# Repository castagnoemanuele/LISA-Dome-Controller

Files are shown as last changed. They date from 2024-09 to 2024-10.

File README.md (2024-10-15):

# LISA-Dome-Controller
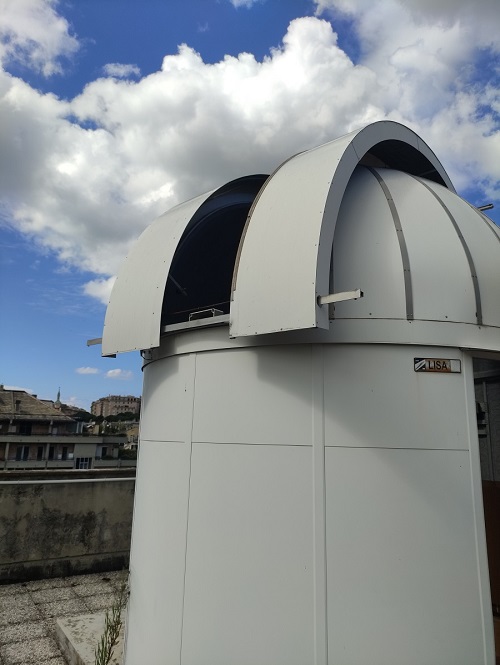
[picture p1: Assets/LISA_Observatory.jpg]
Observatory


This repository contains the project of the controller system for the LISA observatory, located in Genoa. The old controller board was defective and needed to be replaced, and by doing that the system was also modernized and updated to support, for example, the WiFi connection. 

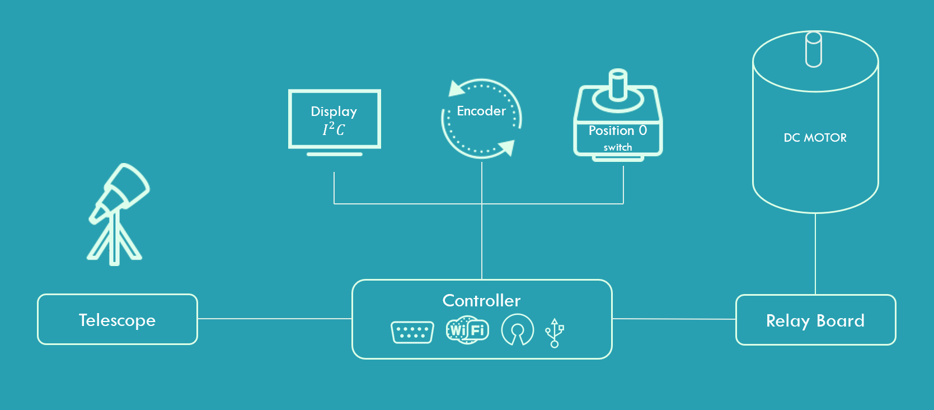
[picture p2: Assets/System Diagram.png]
Diagram

The system is composed of three main sub-systems:
* Telescope
* Motor system
* Control system

## Motor system
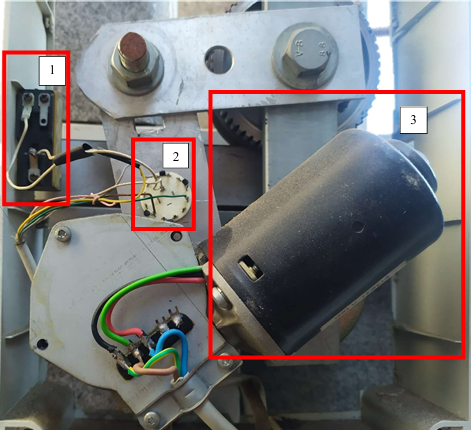
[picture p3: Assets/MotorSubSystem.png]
Motor System


The motor system is composed of three parts:
1. End switch: a simple switch that gets closed at a certain position, which will be referred as "position zero" from now on.
2. Encoder: has three pins (ENCODER1, ENCODER2, ENCODER3) plus a common one. Each one is activated every third of a rotation of the motor
3. 12V DC motor (60w power draw)

The only modification done to this part of the system was a RC circuit connected in parallel with the end switch to filter out noise that was causing problems (ghost change of state of the end switch).
The rotative encoder functioning is is simplified in the following animation:

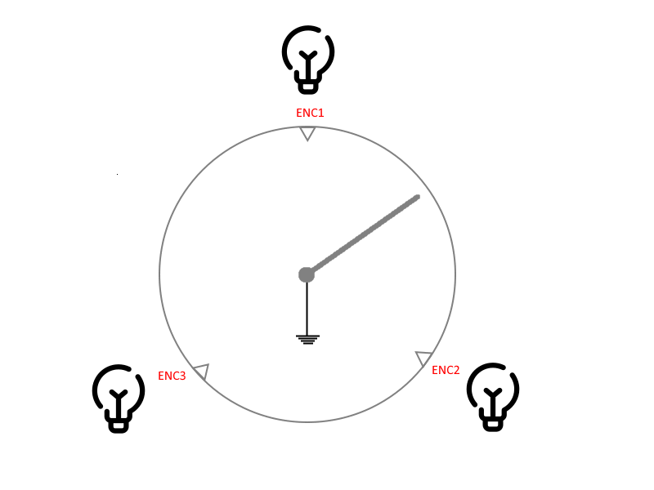
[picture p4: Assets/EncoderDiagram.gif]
Encoder_rotation


In the way it works it is more similar to a rotation counter, but given it's function it will be called encoder.

## Controller system

Composed of four parts:
* Two 12V power supplies, one for the motor and one for the Control system
* The controller board
* The relay board
* The external interface

Here is a more complete overview on the contents of the electrical box:

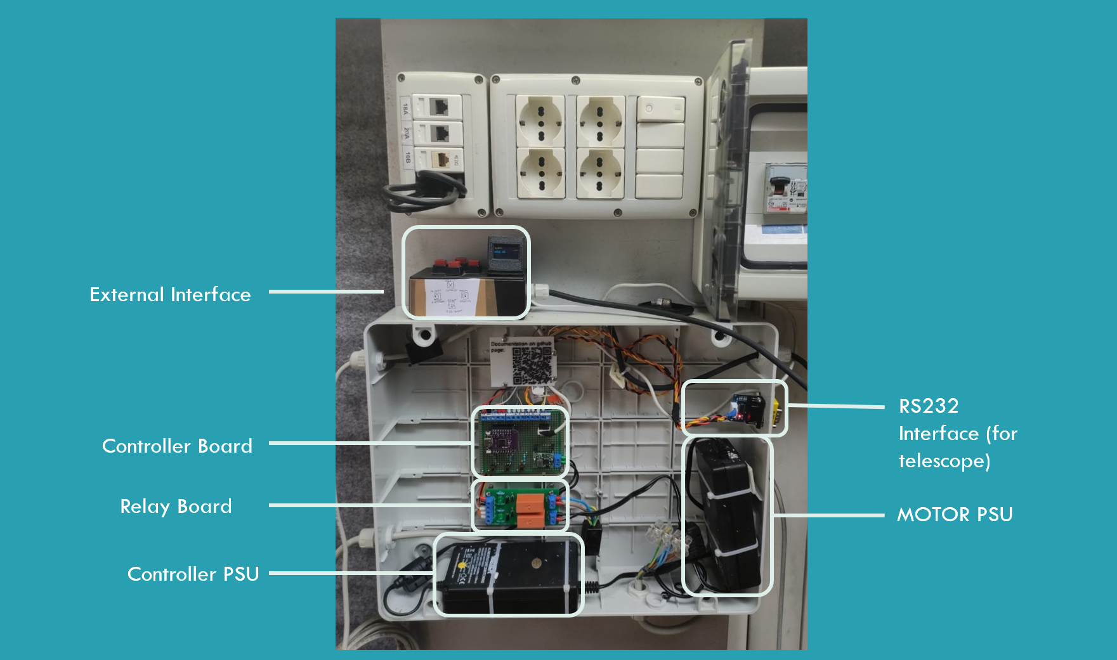
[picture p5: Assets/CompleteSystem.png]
Controller overview


### Relay board
This board has been developed for the purpose of powering the 12V motor. In needs to be able to switch the direction, so two SPDT relays have been used to form an h-bridge. The microcontroller drives the relays throught two npn transistors, and two LEDs have been added to signal which relay is active. The connections are the following:
| PIN | Description|
| ----|---|
|S1 |Selector pin for relay 1, when HIGH turns the coil of relay 1 on|
|S2 |Selector pin for relay 2, when HIGH turns the coil of relay 2 on|
|GND  |Ground, connected to the gnd of the step down on the control board (note that it is isolated from the 12V part of the circuit) 
|5V | Connected to the output of the step down on the control board
|GND(High power part)|Connected to the motor power supply|
|12V | Connected to the motor power supply|
|MOTOR| connection to the motor

The board was custom made using EasyEda and printed by JLCPCB. the PCB has copper traces wide and thick enough to support more than 5A of current. Schematics are avaiable on the apposite folder of this repo.

#### Components of the Relay Board
* 2* RT114005 SPDT relays
* 2* 2N2222 transistors
* 2*220 Ohm Resistor
* 2*1KOhm Resistor
* 2* Flyback diode
* Screw terminal connectors

### Controller board
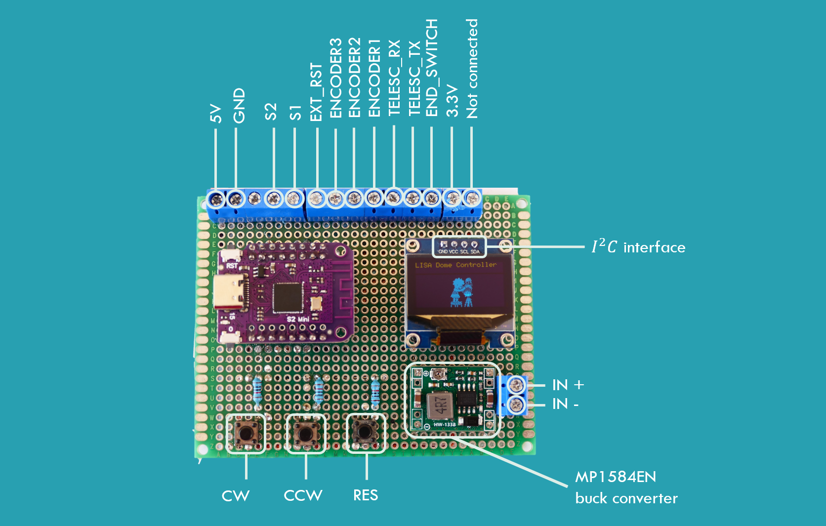
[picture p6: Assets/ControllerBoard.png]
Controller Board Diagram


The controller board hosts the microcontroller and all the interfaces it needs to check the sensors and control the other devices in the system. It also hosts three buttons, which have the same functionality as the ones in the external interface. The microcontroller is a WEMOS ESP32-S2 mini, chosen for the low cost and WiFi support.
the power supply that was present in the electrical box had an output of 12V DC, so a variable step down converter was added, and it is set to 5V and connected to the Vin pin of the microcontroller. 
The I²C interface is powered from the 3.3V pin of the microcontroller and has two 10K pullup resistors, on the back of the perf board.
All the connections are reported in the schematic on the apposite folder. The pinscan be described as it follows:

| PIN | Description|
| ----|---|
|5V| Connection to the Vin pin of the MCU and the OUT+ of the buck converter|
|GND| Ground =0|
|S2 | Connected to the S2 Pin of the relayboard. When high activates relay 2. It is also connected to the External S2 Button of the physical interface|
|S1 | Connected to the S2 Pin of the relayboard. When high activates relay 1. It is also connected to the External S1 Button of the physical interface|
|EXT_RST| Connected to the reset Button of the external interface
|Encoder1,2,3| Connected to the encoder pins (in the motor system|
|TELESC_RX| Connected to the RX pin of the serial to RS232 Adapter|
|TELESC_TX| Connected to the TX pin of the serial to RS232 Adapter|
|END_SWITCH| Connected to the end switch in the motor system!
|3.3V| Connected to the 3.3V pin of the ESP32|
|IN+| Positive Input pin for the buck converter. In the system connected to a 12V PSU|
|IN-| Negative pin for the buck converter. In the system connected to a 12V PSU|

### External interface
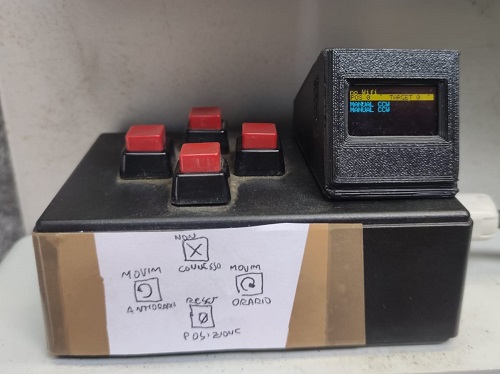
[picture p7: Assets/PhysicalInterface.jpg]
External Interface


The buttons present on the controller board are not avaiable when the electrical box is closed, so to be able to control the Dome posision manually it was necessary to connect the (already present) external keypad and add the external display with a 3d printed enclosure, which was posted on [Thingiverse](https://www.thingiverse.com/thing:3080488) by SteveTecx.

## Notes
The .ino file in the simulator folder was used to simulate the behaviour of the dome to program the firmware outside of the dome. More details are available in my thesis pdf file in the documents folder.

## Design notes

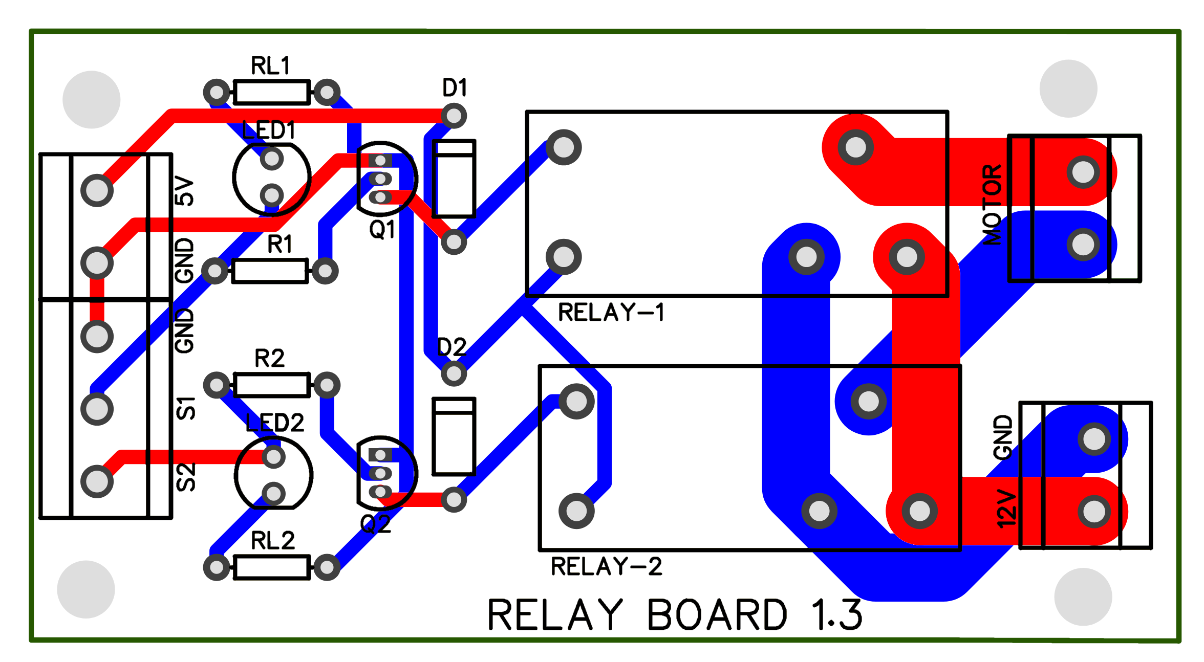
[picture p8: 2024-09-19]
Schematics/RelayBoard schematic .png

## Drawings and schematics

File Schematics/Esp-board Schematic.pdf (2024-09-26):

+3.3V

+3.3V

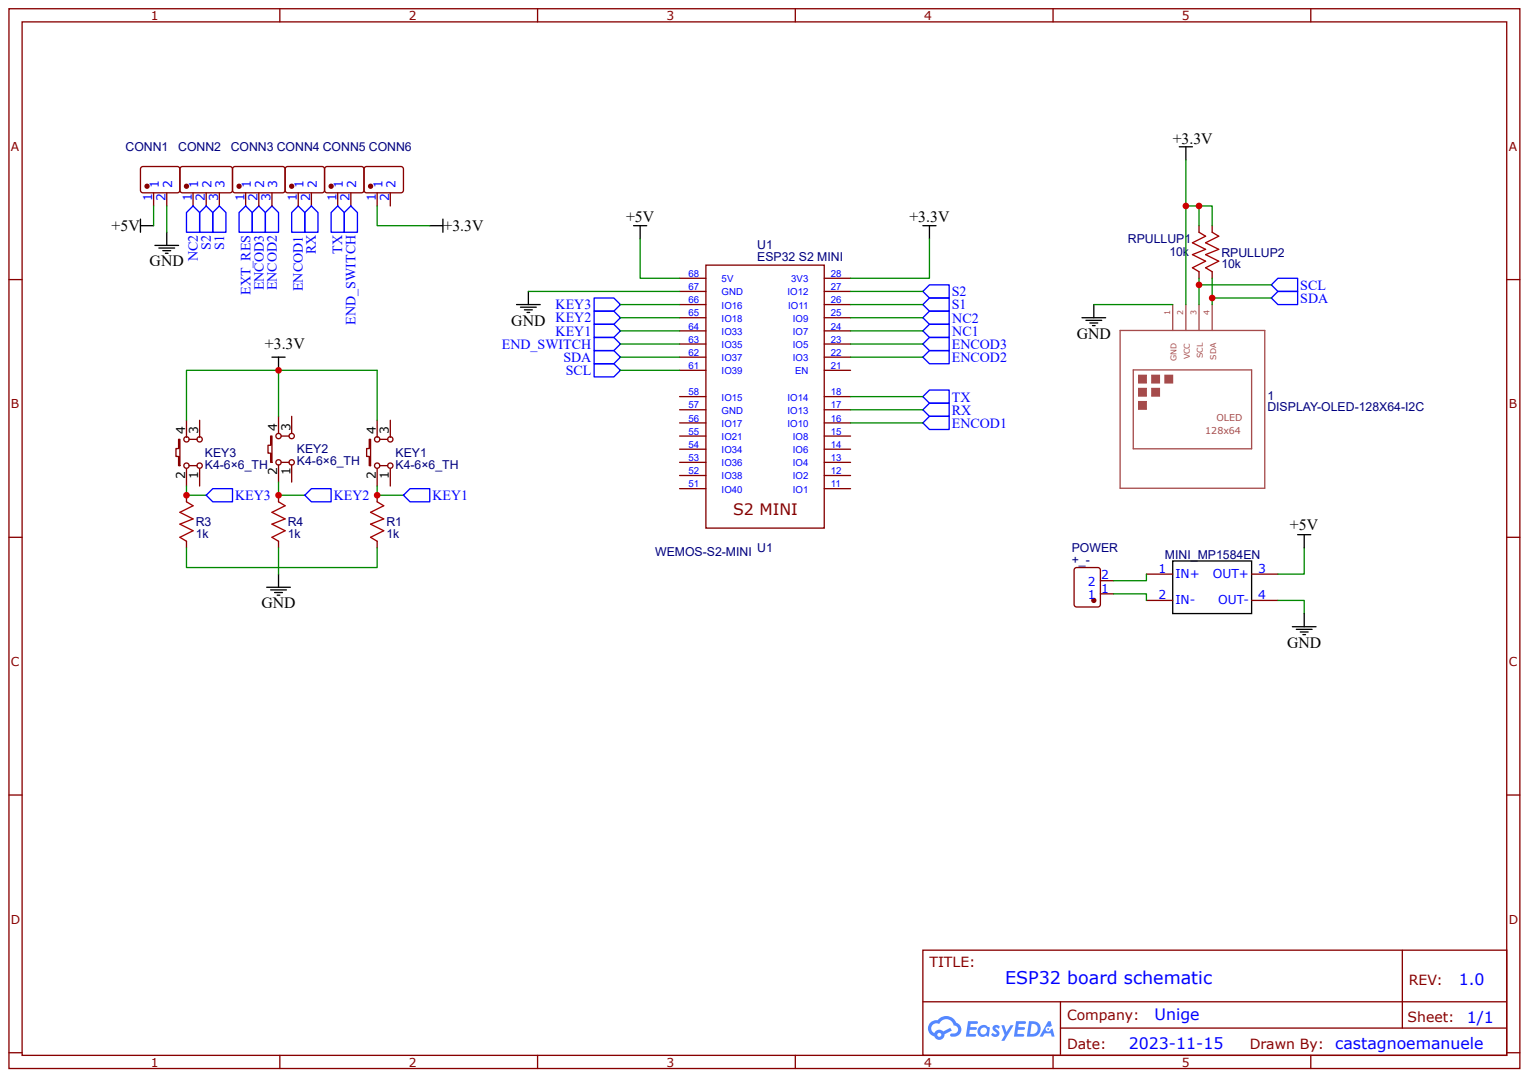
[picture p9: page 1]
TITLE:; ESP32 board schematic; REV: 1.0; Date:; Sheet: 1/1; Company: Unige; ESP32 S2 MINI; WEMOS-S2-MINI U1; S2 MINI; GND; KEY1; KEY2; KEY3; CONN2; DISPLAY-OLED-128X64-I2C; VCC; SCL; SDA; OLED; MINI_MP1584EN IN+; OUT+; OUT- 4; POWER; ENCOD2; ENCOD3; ENCOD1; ENCOD3 ENCOD2; RPULLUP2; RPULLUP1; SCL SDA; END_SWITCH; CONN3; EXT_RES; CONN1; CONN4; CONN5; CONN6; TX END_SWITCH

Drawn By: castagnoemanuele

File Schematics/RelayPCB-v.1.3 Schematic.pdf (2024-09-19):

+5V

+12V | +12V

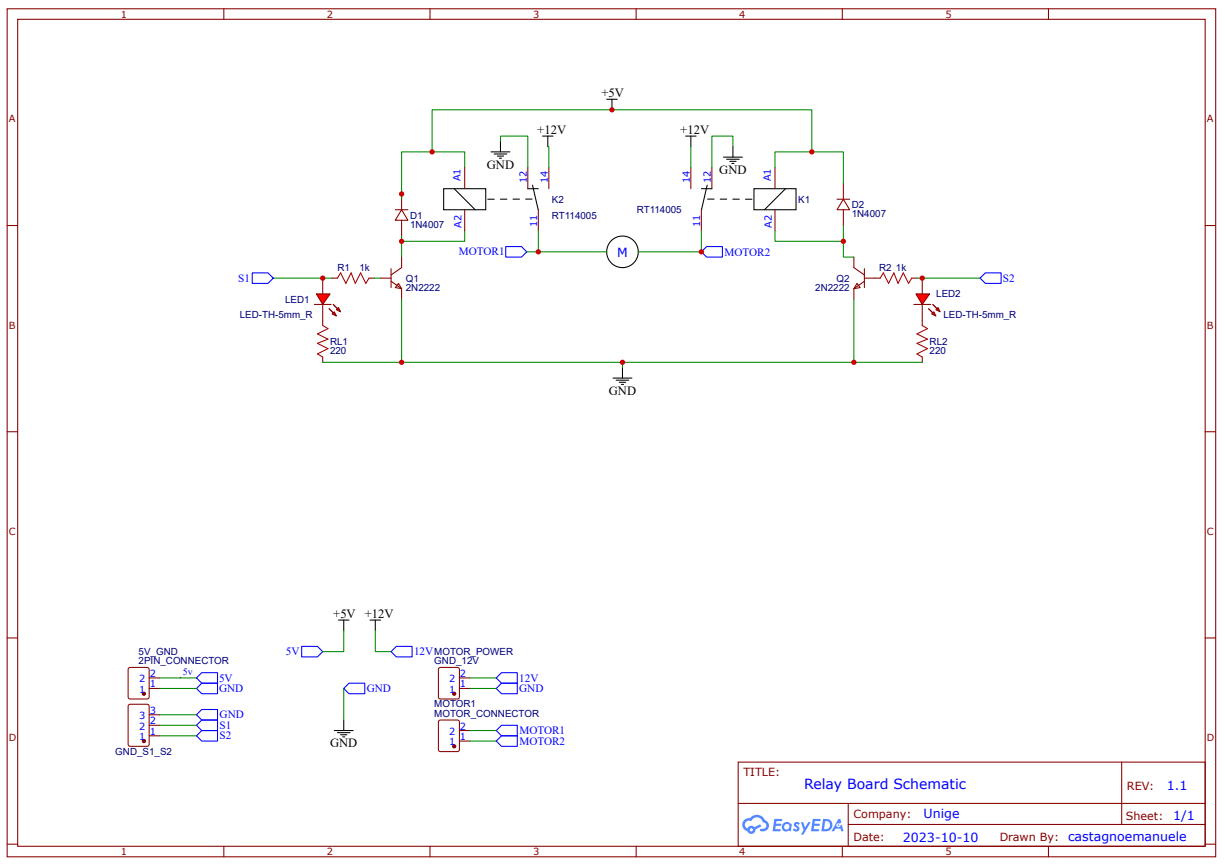
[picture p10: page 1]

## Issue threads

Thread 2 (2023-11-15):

Problem: encoder non being monitored during manual control

castagnoemanuele, 2023-11-15:

Closed 2023-11-20.

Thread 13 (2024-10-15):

Communication with telescope implemented but not functioning

castagnoemanuele, 2024-10-15:
In the `telescope.cpp` file a simple function `checkTelescopePosition` has been implemented to send a request message to the encoder, which should get interpreted by the telescope, which should respond with his position, according to the MEADE serial comm. protocol.

When testing with my computer, I could see that the request message was being sent correctly, and if I replied from my computer with the correctly formatted position, the microcontroller was able to interpret and save the data. This means that at least the physical connection should be working (it has to be noted that to interface the RS232 serial to the computer a USB adapter has been used, but it is not present when the direct connection between the microcontroller and telescope is made).

At the same time, if by using the USB to RS232 serial adapter I send the position request to the telescope (which is `:GR#`) I get the correct data from the telescope, which shoul mean that the telescope is working and also the request is the right one.

The following image is a screenshot of the serial monitor that i opened from my computer to the telescope, and it shows the telescope responding to the request of the position,as stated above.

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

The issue is that when I connect the microcontroller to the telescope and start the telescope position request function (from the serial monitor of the microcontroller's usb port, by typing the letter `p` **no data gets received by the microcontoller**, and after the timeout the execution continues normally.

Things i tried already:

-  Checking physical connection with a multimeter (also voltages)
- adding a `\n` after the `:GR#` message request
-  Checking if the baud rate is set correctly
-  Different serial port

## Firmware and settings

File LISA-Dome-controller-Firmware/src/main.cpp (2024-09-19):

#include <WiFi.h>
#include <WebServer.h>
#include <SPI.h>
#include <Wire.h>
#include <Adafruit_GFX.h>
#include <Adafruit_SSD1306.h>
#include <encoder.h>
#include <config.h>
#include <WiFiManager.h>
#include <telescope.h>
#include <button.h>
#include <Preferences.h>
#include <displayOled.h>


Preferences preferences;
WebServer server(80);

Telescope LISA;
Encoder encoder = {0,0,false,0,0,0,UNKNOWN};


Adafruit_SSD1306 display(SCREEN_WIDTH, SCREEN_HEIGHT, &Wire, OLED_RESET); //initialization of Oled Screen
DisplayOled displayOled;


Button bttReset = {BTT_RST, 0, false,"RESET"};///onboard button to reset the dome's position
Button bttExternalReset = {BTT_EXT_RST, 0, false,"RESET"}; ///external button to reset the dome's position
Button bttClockwise = {BTT_CW, 0, false,"MANUAL CW"};
Button bttCounterClockwise = {BTT_CCW, 0, false,"MANUAL CCW"};
Button limitSwitch = {BTT_END, 0, false, "END REACHED"};


bool needUpdate = false; //flag to update the display only when the button is pressed
static bool commandsPrinted = false; //bool for user interface commands

/// @brief Interrupt Routine handler, sets .pressed attribute according to the reading
/// @return 
void IRAM_ATTR bttClick() {
  bttReset.pressed = digitalRead(BTT_RST);
  bttExternalReset.pressed = digitalRead(BTT_EXT_RST);
  bttClockwise.pressed = digitalRead(BTT_CW);
  bttCounterClockwise.pressed = digitalRead(BTT_CCW);
  limitSwitch.pressed = !digitalRead(BTT_END); //opposite because it is active when low
  needUpdate= true;
}


void IRAM_ATTR encoderTick() {
  encoder.hasChanged=true;
}


bool dataSaveNecessary=false;
bool telescopeCheckNecessary=false;
hw_timer_t *timerEPROM = NULL;
hw_timer_t *timerTelescope = NULL;

/// @brief Interrupt Routine handler, Checks the timer to save the position periodically
void IRAM_ATTR onTimerEPROM(){
  dataSaveNecessary=true;
}
/// @brief Interrupt Routine handler, Checks the timer to check the telescope position periodically
void IRAM_ATTR onTimerTelescope(){
  telescopeCheckNecessary=true;
}


void setup()
{
  ////////////////////////SERIAL COMMUNICATION INIT/////////////////////
  Serial.begin(9600); 
  Serial1.begin(9600,SERIAL_8N1,TX_PIN,RX_PIN); ///serial port to communicate with telescope
  /////////////////BUTTON/PIN INITIALIZATION////////////////////////////
  pinMode(LED_BUILTIN, OUTPUT);      // set the LED pin mode
  pinMode (bttReset.PIN, INPUT_PULLDOWN);
  pinMode (bttExternalReset.PIN, INPUT_PULLDOWN);
  pinMode (bttClockwise.PIN, INPUT_PULLDOWN);
  pinMode (bttCounterClockwise.PIN, INPUT_PULLDOWN);
  pinMode (limitSwitch.PIN, INPUT_PULLUP);
  pinMode (S1_PIN, OUTPUT);
  pinMode (S2_PIN,OUTPUT);
  digitalWrite(S1_PIN, LOW);
  digitalWrite(S2_PIN, LOW);
  
  attachInterrupt (limitSwitch.PIN, bttClick, FALLING);
  attachInterrupt (bttReset.PIN, bttClick, CHANGE);
  attachInterrupt (bttClockwise.PIN, bttClick, CHANGE);
  attachInterrupt (bttCounterClockwise.PIN, bttClick, CHANGE);
  attachInterrupt (bttExternalReset.PIN, bttClick, CHANGE);
  /////////////////////////ENCODER PINS INITIALIZATION////////////////////////////////
  pinMode(ENCODER1, INPUT_PULLUP);
  pinMode(ENCODER2, INPUT_PULLUP);
  pinMode(ENCODER3, INPUT_PULLUP); 
  attachInterrupt(digitalPinToInterrupt(ENCODER1), encoderTick, FALLING);
  attachInterrupt(digitalPinToInterrupt(ENCODER2), encoderTick, FALLING);
  attachInterrupt(digitalPinToInterrupt(ENCODER3), encoderTick, FALLING);

  ////////////////////////OLED INITIALIZATION//////////////////////////
  displayOled.initDisplay(display, encoder, LISA);

    ////////////////////////////WIFI INITIALIZATION//////////////////////////
    // start by connecting to a WiFi network
    //WiFiManager wifiManager; //REMOVED AFTER INITIAL SETUP
    //wifiManager.resetSettings(); //TO CLEAN SETTINGS
    //wifiManager.autoConnect("AutoConnectAP");
    

    ///Wait for Connection while also printing on the display
    // for (int i = 0; i<12;i++)
    // {
    //   if (WiFi.status() != WL_CONNECTED) {
    //     delay(500);
    //     Serial.print(".");
    //     displayMessage("......");
    //   }
    // }

  if (WiFi.status() == WL_CONNECTED) 
  {
    //Blink 3 times to signal wifi connection
    for (int i=0; i<3; i++){
      digitalWrite(LED_BUILTIN, HIGH);
      delay(200);
       digitalWrite(LED_BUILTIN, LOW);
      delay(100);
    }
    
    
    Serial.println("");
    Serial.println("WiFi connected.");
    Serial.println("IP address: ");
    Serial.println(WiFi.localIP());
    
  }
  else{displayOled.FirstRow="no Wifi";}
  
  ////////////////////////ENCODER STATUS SETUP//////////////////////////////
  preferences.begin("LISA", true); //start preferences in readonly mode
  encoder.currentPosition = preferences.getInt("currentPosition", 0); //read values from EPROM and set them to the encoder variables
  encoder.fullRotation= preferences.getInt("fullRotation",0);
  //check if we have any data on the fullRotation
  if(encoder.fullRotation==0){
    Serial.println("No full rotation data found, counting now");
    displayOled.displayMessage("COUNT TICKS",display);
    countTicksFullRotation(encoder,bttReset,limitSwitch,preferences);
  }
  Serial.print("Current position: ");
  Serial.println(encoder.currentPosition);
  encoder.currentDegrees = convertTicksToDegrees(encoder.currentPosition, encoder);
  Serial.print("     In degrees: ");
  Serial.println(encoder.currentDegrees);
  Serial.print("Number of encoder clicks for a full rotation: ");
  Serial.println(encoder.fullRotation);
  preferences.end();

  displayOled.printPositionStatus(display, encoder, LISA); //refresh position with the new data from the EPROM

  ////////////////////////////TIMER FOR SAVING DATA/////////////////////////////
  timerEPROM = timerBegin(0, 8000, true);
  timerAttachInterrupt(timerEPROM, &onTimerEPROM, true);
  timerAlarmWrite(timerEPROM, 3000000, true); //setting a timer to save encoder data to EPROM every 5 minutes
  timerAlarmEnable(timerEPROM); //Just Enable the timer

  //////////////////////////TIMER FOR TELESCOPE CHECK//////////////////////////
  timerTelescope = timerBegin(1, 8000, true);
  timerAttachInterrupt(timerTelescope, &onTimerTelescope, true);
  timerAlarmWrite(timerTelescope, 100000, true); //setting a timer to check the telescope position every 10 seconds
  //timerAlarmEnable(timerTelescope); //Just Enable the timer

  

}

void loop()
{
  if (limitSwitch.pressed)
  {
    if(encoder.currentPosition!=0){
      Serial.println("End of run reached");
    }
    encoder.currentPosition = 0;
    encoder.currentDegrees = 0;
  }
  ////////////////////////////MANUAL CONTROL///////////////////////////
  //when the reset button is pressed, the motor starts spinning clockwise until the limit switch stops it
  if (bttReset.pressed || bttExternalReset.pressed)
  {
    displayOled.displayMessage(bttReset.message,display);
    resetPosition(encoder, bttReset, limitSwitch);
    displayOled.displayMessage("END of RUN",display);
    displayOled.printPositionStatus(display, encoder, LISA);
  }
  //turn on relays according to the button status
  digitalWrite(S1_PIN, bttClockwise.pressed);
  digitalWrite(LED_BUILTIN, bttClockwise.pressed);

  if (bttClockwise.pressed & needUpdate)
  {
    displayOled.displayMessage(bttClockwise.message,display);
    needUpdate = false;
  }
  digitalWrite(S2_PIN, bttCounterClockwise.pressed);
  digitalWrite(LED_BUILTIN, bttCounterClockwise.pressed);
  if (bttCounterClockwise.pressed & needUpdate)
  {
    displayOled.displayMessage(bttCounterClockwise.message,display);
    needUpdate = false;
  }
  ///////////////////////UPDATE POSITION//////////////////////////////
  if (encoder.hasChanged)
  {
    //when movement is detected, we first check the direction, and then update the position
    checkEncoder(encoder);
    encoder.hasChanged = false;
    updatePosition(encoder);
    displayOled.printPositionStatus(display, encoder, LISA);
  }
  //server.handleClient(); for future remote control features
  //////////////////DATA SAVE//////////////////////////////
  if (dataSaveNecessary)
  {
    saveData(encoder.currentPosition, "currentPosition", preferences); //save the position to the EEPROM every 5 minutes
    dataSaveNecessary = false;
    displayOled.displayMessage("POS SAVE",display);
  }
  ///////////////////////TELESCOPE CHECK////////////////////////
  if (telescopeCheckNecessary)
  {
    displayOled.displayMessage("TEL CHECK",display);
    //LISA.checkTelescopePosition();
    Serial.println("Checking telescope position");
    telescopeCheckNecessary = false;
  }
  //////////////////////SERIAL COMM TEST/////////////////////////////
  // while (Serial1.available() > 0) {
  //   char inByte = Serial1.read();
  //   Serial.write(inByte);
  //   Serial1.write(inByte);
  //   displayMessage(String(inByte));
  // }



  
  ////////////////////////////Serial terminal interface to test functions////////////////////////
  if (!commandsPrinted) {
    Serial.println("\nAvailable commands:");
    Serial.println("p: check telescope position");
    Serial.println("r: reset position");
    Serial.println("c: count ticks for a full rotation");
    Serial.println("s: save data to EEPROM");
    Serial.println("t: print position data on serial");
    Serial.println("z: force update of position data on display");
    Serial.println("w: display message test");
    Serial.println("g: save full rotation data to EEPROM");
    commandsPrinted = true;
  }
  if (Serial.available() > 0)
  {
    char inByte = Serial.read();
    if (inByte == 'p')
    {
      LISA.checkTelescopePosition();
      displayOled.printPositionStatus(display, encoder, LISA);
    }
    if(inByte == 'r')
    {
      resetPosition(encoder, bttReset, limitSwitch);
    }
    if (inByte == 'c')
    {
      countTicksFullRotation(encoder, bttReset, limitSwitch, preferences);
    }
    if (inByte == 's')//force save data to EEPROM
    {
      saveData(encoder.currentPosition, "currentPosition", preferences);
    }
    if (inByte == 't')//Print all position data
    {
      Serial.println("Encoder current position: ");
      Serial.println(encoder.currentPosition);
      Serial.println("Encoder Current degrees: ");
      Serial.println(encoder.currentDegrees);
      Serial.println("Encoder full rotation ticks: ");
      Serial.println(encoder.fullRotation);

      Serial.println("Telescope position: ");
      Serial.println(LISA.getTelescopePosition());
    }
    if (inByte == 'z')
    {
      Serial.println("Updating display position");
      displayOled.printPositionStatus(display, encoder, LISA);
    }
    if(inByte == 'w')
    {
      displayOled.displayMessage("test",display);
      displayOled.displayMessage("COUNT TICKS",display);
    }
    if (inByte== 'g'){
      saveData(360,"fullRotation",preferences);
    }
    else
    {
      Serial.println("Command not recognized");
      commandsPrinted = false;
    }
  }
}

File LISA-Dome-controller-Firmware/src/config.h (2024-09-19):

/**
 * @file config.h
 * @brief Configuration file for LISA Dome Controller.
 *
 * This file contains the pin definitions and configuration settings for the LISA Dome Controller.
 * It includes pin assignments for LEDs, buttons, encoders, I2C communication, and the OLED display.
 
 */

#define LED_INTEGRATED 15 ///LED pin
#define S1_PIN 11 ///Selector pin 1 for the relays
#define S2_PIN 9 ///Selector pin 2 for the relays
#define SCL_PIN 39 ///I2C SCL pin
#define SDA_PIN 37 ///I2C SDA pin
#define BTT_CW 18 ///Clockwise button pin
#define BTT_CCW 16 ///Counter Clockwise button pin
#define BTT_RST 33 ///position Reset button pin
#define BTT_EXT_RST 7///external position reset button
#define BTT_END 35 ///Limit switch button pin
#define ENCODER1 10 ///Encoder pin
#define ENCODER2 3 ///Encoder pin
#define ENCODER3 5 ///Encoder pin
#define TX_PIN 14 ///Telescope TX pin
#define RX_PIN 13 ///Telescope RX pin


#define SCREEN_WIDTH 128 /// OLED display width, in pixels
#define SCREEN_HEIGHT 64 /// OLED display height, in pixels
#define OLED_RESET -1 /// Reset pin # (or -1 if sharing Arduino reset pin)
#define SCREEN_ADDRESS 0x3C ///Oled Screen Address for initialization

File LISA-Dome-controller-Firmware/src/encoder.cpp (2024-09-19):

/**
 * @file encoder.cpp
 * @brief This file contains the implementation of functions to handle the encoder data, update the position of the dome, reset the position, count ticks for a full rotation, convert ticks to degrees, and save data to EEPROM.
 * 
 * The functions included are:
 * - checkEncoder(Encoder& encoder1)
 * - updatePosition(Encoder& encoder1)
 * - resetPosition(Encoder& encoder1, Button& resetButton, Button& limitSwitch)
 * - countTicksFullRotation(Encoder& encoder1, Button& resetButton, Button& limitSwitch, Preferences& preferences)
 * - convertTicksToDegrees(int ticks, Encoder& encoder1)
 * - saveData(int data, const char *address, Preferences& preferences)
 * 
 * These functions are used to manage the state and position of the encoder, update the dome's position, reset the dome's position, count the number of ticks for a full rotation, convert ticks to degrees, and save data to EEPROM.
 * 
 * 
 */
#include "config.h"
#include "encoder.h"
#include <Preferences.h>


#include <esp32-hal-gpio.h>
#include "button.h"


/// @brief Handles encoder Data
/**
 * Checks the state of the encoder by comparing which sector is active relative to the sector that
 * was active in the previous iteration. This way it also detects the direction of rotation.
 * @param encoder1 The Encoder object to be checked.
 */
void checkEncoder(Encoder& encoder1){
  if(encoder1.oldSector!=encoder1.newSector){
  //save the old sector
  encoder1.oldSector=encoder1.newSector;}
  //find the new sector
  if(digitalRead(ENCODER1)==LOW){
    encoder1.newSector=1;
  }
  if(digitalRead(ENCODER2)==LOW){
    encoder1.newSector=2;
  }
  if(digitalRead(ENCODER3)==LOW){
    encoder1.newSector=3;
  }

  encoder1.hasChanged=false;

  /////////DETECT DIRECTION////////
  //we do this by comparing the old sector with the new sector
  switch (encoder1.newSector){
    case 1:
    if (encoder1.oldSector==2){
      encoder1.direction=CCW;
    }
    if (encoder1.oldSector==1){
      encoder1.direction=CW;
    }
    break;
    case 2:
    if (encoder1.oldSector==3){
      encoder1.direction=CCW;
    }
    if (encoder1.oldSector==1){
      encoder1.direction=CW;
    }
    break;
    case 3:
    if (encoder1.oldSector==1){
      encoder1.direction=CCW;
    }
    if (encoder1.oldSector==2){
      encoder1.direction=CW;
    }
    break;
  }
}

/// @brief Updates the position of the dome according to the rotation of the encoder
/// @param encoder1 the encoder object
/// @param resetButton the button object
/// @param limitSwitch the button object
void updatePosition(Encoder& encoder1){
  if(encoder1.newSector!=encoder1.oldSector){
      Serial.print(encoder1.oldSector);
      Serial.print("->");
      Serial.println(encoder1.newSector);
      /////////////UPDATE POSITION////////////////
      if (encoder1.direction==CW){
        encoder1.currentPosition++;
      }
      else if (encoder1.direction==CCW){
        encoder1.currentPosition--;
      }
      Serial.print("Current encoder position in ticks: ");
      Serial.print(encoder1.currentPosition);
      
      //Convert data to degrees 
      encoder1.currentDegrees = convertTicksToDegrees(encoder1.currentPosition, encoder1);

      Serial.print("  In degrees: ");
      Serial.println(encoder1.currentDegrees);
      Serial.println("");

      
    }
}
  

/// @brief call this function to disable all controls and wait for the dome to return to the original position
/**
 * Resets the position of the dome.
 *
 * @param encoder1 The encoder object.
 * @param resetButton The button used for resetting the position.
 * @param limitSwitch The limit switch used for detecting the end position.
 */
void resetPosition(Encoder& encoder1, Button& resetButton, Button& limitSwitch){
  resetButton.pressed=false;
  
  if (encoder1.currentPosition==0){
    Serial.println("Dome is already in position 0.");
    return;
  }
  
  Serial.println("Resetting position to 0.");
  
  while(!limitSwitch.pressed){
    //check if we need a clockwise or counterclockwise rotation to get to the limit switch faster
    if(encoder1.currentPosition<0){ 
      digitalWrite(S1_PIN,HIGH);
    } else if (encoder1.currentPosition>0){
      digitalWrite(S2_PIN,HIGH);
    }
    delay(100);
  }
  //when we reach position zero the motor gets shut off
  digitalWrite(S1_PIN,LOW);
  digitalWrite(S2_PIN,LOW);
  Serial.println("Dome has returned to position 0.");
  //Update current position information
  encoder1.currentPosition = 0;
  encoder1.currentDegrees = convertTicksToDegrees(encoder1.currentPosition, encoder1);

}

/// @brief Counts how many Ticks happen to make a full rotation of the dome and saves the data to the EEPROM
/// @return number of ticks counted 
long countTicksFullRotation (Encoder& encoder1, Button& resetButton, Button& limitSwitch, Preferences& preferences)
{
  //bring the dome to the starting position
  resetPosition(encoder1, resetButton, limitSwitch);
  long ticks=0;
  Serial.println("Starting rotation to count fullRot.");
  digitalWrite(S1_PIN,HIGH);//initiate rotation
  delay(1000); //wait for the dome to start rotating
  while (limitSwitch.pressed==false){
    //count how many updates happen to the encoder
    if(encoder1.hasChanged){
      checkEncoder(encoder1);
      if(encoder1.oldSector != encoder1.newSector){
        ticks++;
        Serial.println(ticks);
      }
      encoder1.hasChanged=false;
    }
  }
  //Turn off the motor after the dome has made a full rotation
  digitalWrite(S1_PIN,LOW);
  Serial.print("Ticks counted:");
  Serial.println(ticks);
  saveData(ticks, "fullRotation", preferences);
  
  return ticks;
}
/// @brief Convert a number of ticks with a porportion to the equivalent in degrees keepin
/// @param ticks number of ticks to be converted
/// @param encoder1 the encoder object, used to get the full rotation data
/// @return the number of tick converted to degrees, considering the full rotation data
int convertTicksToDegrees(int ticks, Encoder& encoder1){
  int degrees;
  if (encoder1.fullRotation==0){
    Serial.println("Full rotation data not found.");
    return 0;
  }
  if(ticks<0){
    return ((ticks*360)/(encoder1.fullRotation )) + 360;
  }
  return (ticks*360)/(encoder1.fullRotation);
}
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

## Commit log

2023-10-22 Added first interrupt handler
2023-10-29 Better button structure and minor modifications
2023-11-08 Finished Manual control via button, with simple return to position of end of run
2023-11-09 added first simple encoder implementation
2023-11-12 Added reading currentPosition from EPROM
2023-11-13 added timer for autosave to Eprom and minor modifications
2023-11-16 fix issues #2 #3 and other minor improvements
    [main.cpp]
2024-03-03 Modularization and addition of WiFiManager (issue #17)
    [config.h, encoder.cpp, main.cpp]
2024-03-03 Modularization and addition of WiFiManager (issue #7)
    [config.h, encoder.cpp, main.cpp]
2024-04-15 General improvements to #5 #8 #1 and solved #4
    [encoder.cpp, main.cpp, telescope.cpp]
2024-04-18 fixed errors in EPROM saving
    [encoder.cpp, main.cpp, telescope.cpp]
2024-04-21 probably solved issues #5 #8, improvemnts on #6 and #1
    [encoder.cpp, main.cpp, telescope.cpp]
2024-05-01 fixed one display error (issue #9) and made the display a class(issue #10)
    [displayOled.cpp, encoder.cpp, main.cpp]
2024-05-03 added timer for periodic telescope check and other minor improvemnts
2024-09-19 Schematics and Documents added
2024-09-25 added Controller board diagram
